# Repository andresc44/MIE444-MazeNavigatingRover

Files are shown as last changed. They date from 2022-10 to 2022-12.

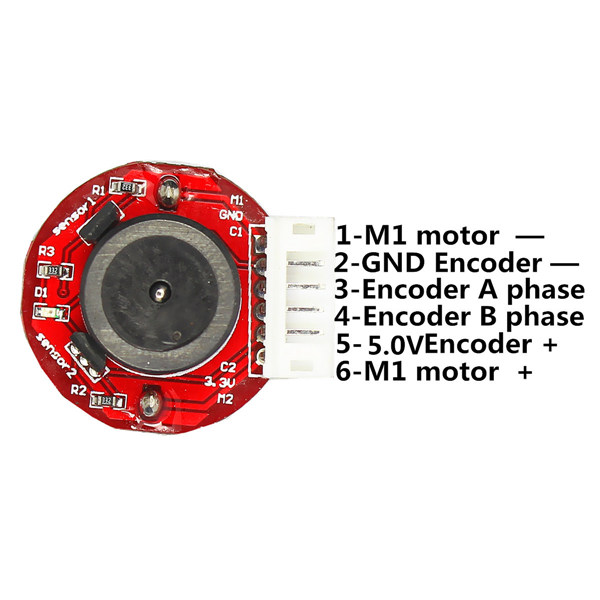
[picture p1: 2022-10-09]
Documents/SampleCodes/Encoder/6V_DC_Motor_Encoder_Wiring.jpg

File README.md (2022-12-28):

# MazeNavigatingRover
**Mechanical Engineering students of MIE444 at the University of Toronto**

*Andres Cervera Rozo, Christopher Tong, Liam Toner, Nathalie Cristofaro*

## Description
Course project to autonomously navigate through a maze and retrieve a wooden block

***Enter Summary of project, contest, 3 milestones, and key words of our design***
- 360 degree Lidar
- 3 Omni wheels for holonomic movement
- Hector SLAM for mapping area
- AMCL and move_base for localization and navigation to various waypoints
- Gazebo simulation of maze for parameter tuning
- Servo motor to retreive a block based on a Time of Flight sensor
- 3 DC Motors with encoders for straight motion tuning
- LED feedback
- Laser-cut plywood chassis
- 2 Arduino UNOs for rapid microcontroller response
- Raspberry Pi for communication to remote ROS Master
- 3D-printed sensor mounts and block retrieval mechanism

[Final document](https://github.com/andresc44/MIE444-MazeNavigatingRover/blob/main/Documents/MIE444%20Final%20Report.pdf)

[Project Proposal](https://github.com/andresc44/MIE444-MazeNavigatingRover/blob/main/Documents/MIE444_Proposal_Team_11.pdf)

## Autonomous Rover


## Course Maze


Please view this video to view the successful completion of the first milestone
[Trial Video](https://drive.google.com/file/d/1N6VmtPNb4CGCVo7hIk6XC2uphVTjW1oM/view?usp=sharing)

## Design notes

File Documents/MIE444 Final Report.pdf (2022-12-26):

## MIE444 - Mechatronics Principles

## Final Project Report

December 16th, 2022
Group 11

Liam Toner (1005178754)
Chris Tong (1005661874)
Andres Cervera-Rozo (1005469217) Nathalie Cristofaro (1004838009)

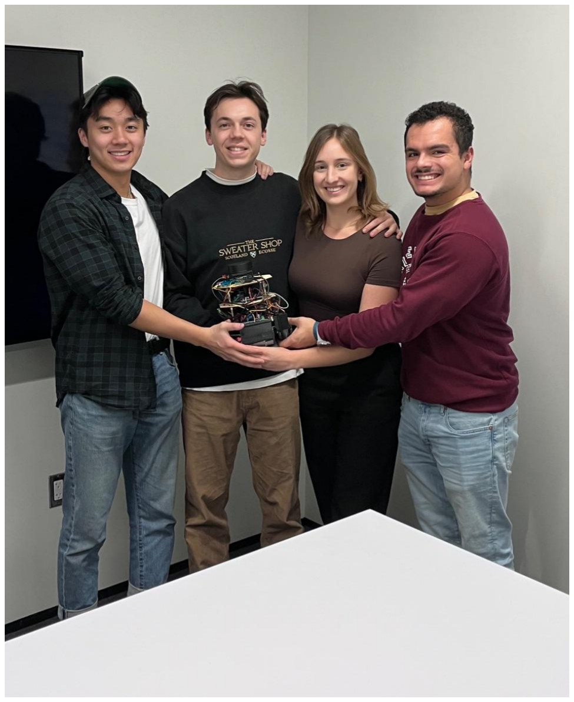
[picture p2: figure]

Link to milestone 3 videos: https://drive.google.com/drive/folders/1ZH4aUpbSbr8QGiYuTMWXnF71OBrIfj4q?usp=s haring (https://drive.google.com/drive/folders/1ZH4aUpbSbr8QGiYuTMWXnF71OBrIfj4q?usp=sharing)

## Table of Contents

1.0 Executive Summary | 2
2.0 Detailed Rover Control Strategy | 2
2.1 Obstacle Avoidance Strategy | 3
2.1.1 Component Software and Integration | 3
2.1.2 Movement Strategy | 4
2.1.3 Calculating and Generating Movement Commands | 4
2.1.4 Milestone One Challenges and Solutions | 5
2.2 Localization and Navigation Strategy | 5
2.2.1 Creating Simulation in Gazebo | 6
2.2.2 Introduction to Hector SLAM | 8
2.2.3 AMCL ROS Package | 8
2.2.4 Sending Navigation Goals Node | 9
2.2.5 Move_base ROS Package | 9
2.2.6 Trajectory Planner, a Move_base Sub-Package | 9
2.3 Block Delivery Strategy | 10
2.3.1 Design of Block Retrieval Mechanism | 10
2.3.2 Programming Block Pickup and Dropoff | 11
2.4 Integration Strategy | 12
3.0 Final Results | 14
3.1 Obstacle Avoidance | 14
3.2 Localization | 14
3.3 Pick-up and Delivery of the Load | 14
3.4 Integration | 15
4.0 Discussion | 17
4.1 Obstacle Avoidance and Localization | 17
4.2 Robot Design and Assembly | 17
4.3 Electrical System Discussion | 18
4.4 Gazebo Simulation | 19
5.0 References | 20

## 1.0 Executive Summary

This report investigates the performance of group 11’s robot for the Mechatronics Principles course term project. The project consisted of designing, building, and programming a robot that would complete three milestones throughout the semester.

The first milestone was obstacle avoidance, where the robot had to travel 20ft in a maze without hitting walls. The team’s robot completed this challenge successfully, with the robot only needing one adjustment to continue on its course. In order to complete this achievement, the team used a Raspberry Pi, LiDAR sensor, and an Arduino Uno to control the robot systems, with the Raspberry Pi acting as the main controller. The Raspberry Pi and LiDAR communicated with a remote PC through the ROS framework to determine the direction and response of the robot. The PC would send PWM values to the Arduino Uno through the Pi to control the direction and speed of the omni-wheels.

The team was not able to complete the second milestone, which involved navigating and localizing in the maze, due to the short timeline available to debug the Hector SLAM mapping package. However, the initial plan to complete this task was to model the robot as a URDF file, use Hector SLAM to map the maze, and use AMCL to create a particle distribution probability map that would determine the final location of the robot by comparing a live map with the pre-generated reference map. A Gazebo simulation was intended to be used for debugging and as a back-up plan to show the robot localization in a simulation.

The third milestone combined the previous milestones and added the additional challenge of locating and delivering a block. The robot was able to successfully complete the third milestone by combining the original idea for milestone two with some alterations to facilitate the programming. A sweeping mechanism was added to the robot frame, which was able to efficiently acquire, contain, and deliver the block to a drop off location. The robot was also capable of localizing at the four-way intersection in the maze.

Overall, consistent with the agreed upon goals at the start of the project, the team learned a great deal about Hector SLAM, ROS architecture, and other common packages and frameworks used commonly in the mechatronics industry. The physical design of the robot was very successful, whereas programming posed a few challenges that would have been resolved with more time, or if the team had chosen a simpler robot design and concept for the project.

## 2.0 Detailed Rover Control Strategy

If the reader is not familiar with ROS, in order to comprehend the terminology in the following sections of the report, the team has recommended the following online references which provide definitions for terms such as node, topic, publish, subscribe, etc. and general information on the ROS framework used for this project.

Online resources:
[1] https://wiki.ros.org/ROS/Introduction
[2] https://ros.org/

## 2.1 Obstacle Avoidance Strategy

In order to complete milestone one, the robot needed to achieve an efficient obstacle avoidance strategy to navigate through the maze without colliding into walls. The robot accomplished milestone one using a LiDAR sensor, remote master PC, Raspberry Pi, and Arduino to collect and send data to the motor controllers which controlled three DC motors with encoders, each attached to an omni-wheel.

2.1.1 Component Software and Integration
The Raspberry Pi is essentially a small computer that is compatible with multiple distributions of the Linux operating system. The team’s Raspberry Pi used the Ubuntu 20.04 distribution in conjunction with the Robot Operating System (ROS) framework. The ROS framework is a free open-source software that defines the various tools, libraries, and interfaces used to connect to the actuators and control the systems of a robot. The use of this framework facilitated the integration of a LiDAR sensor into the robot design, which would typically be very complicated without utilizing pre-built libraries. The Raspberry Pi comes with an integrated wifi connectivity option, which the team used to connect to an external PC. The external PC used by the team was dual-booted in order to use Linux as a second operating system. The PC’s Ubuntu system also had the ROS framework installed. Once the Raspberry Pi and external PC were confirmed to be on the same wifi network, the bashrc files were configured to link the IP addresses of both devices; the PC was set as the master and the Raspberry Pi as the slave so that the Raspberry Pi could be controlled from the PC.

The LiDAR was connected to the Raspberry Pi using a standard USB cable. The Pi would take in the raw LiDAR data and convert this data into a Laser Scan message which was published to a /scan topic. This procedure would transform the data into a global variable that could be read by the PC. The PC accessed this data by subscribing to the /scan topic.

2.1.2 Movement Strategy
The LiDAR sensor gathered data by taking 720 distance and angle measurements during one full 360° rotation. This data was sorted into a 720 element array which was divided into a 12 section circular map, as seen in Figure 1.

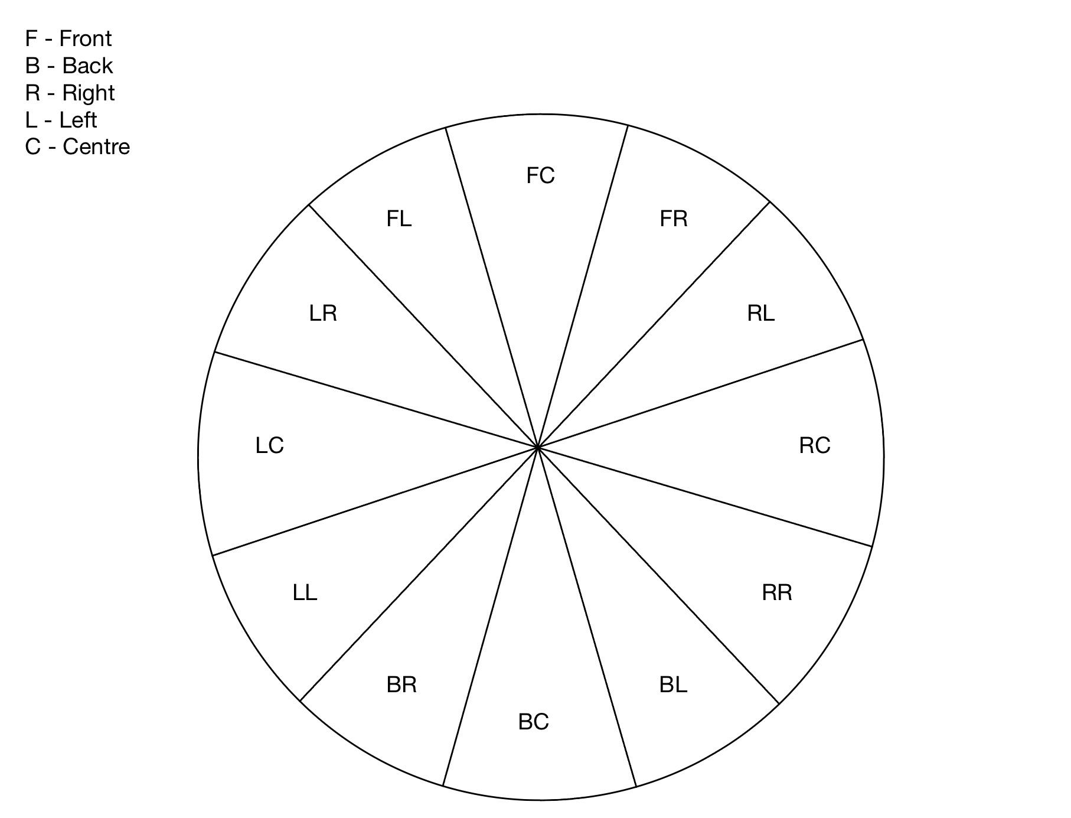
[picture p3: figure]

Figure 1: LiDAR Map Visualization.

Each slice of the map contained 60 data points that helped the robot determine if an obstacle was present in the region. The robot was designed to move in such a way where the front-center slice was always the preferred movement direction. If an obstacle was not detected by the LiDAR in this region, the Arduino would send a “move straight” command to the motor drivers and the robot would move forward. If an obstacle was present in the front-center slice, the robot would check if obstacles were present in the next two outer slices, and continue around the circle until an obstacle was not detected in one of the slices. Once a slice with no obstacle was found, the Arduino would send a “rotate” command, and the robot would align the front-center slice with the slice that contained no obstacles before moving straight. If every slice contained an obstacle, the robot would rotate and move in the direction of the furthest obstacle.

2.1.3 Calculating and Generating Movement Commands

The output of the obstacle avoidance algorithm used in the robot movement strategy was a command velocity that would either indicate that the robot needed to rotate or drive straight. As there were three omni-wheels and because the wheels were multi-directional, the node that received the command velocity performed matrix multiplications in order to convert the command velocities into a pulse width modulation (PWM) magnitude and rotation direction for each wheel based on their geometric configuration. These calculations were done on the PC and transmitted to the Raspberry Pi, which was connected to the Arduino using serial communication. The Pi ran a script to ensure that the Arduino was subscribed to the relevant topic, and published data accordingly. The gathered PWM signals and rotation directions were combined into a smaller 6 item array message that was received by the Arduino. 1s and 0s in the message would indicate whether the wheels would need to turn clockwise or counter-clockwise, respectively. These direction commands were sent to the motor controller via digital write pins on the Arduino. The PWM signals in the message were sent to the motor’s enable pins via the analog write pins on the Arduino, and these signals would determine the motor speed. The LiDAR data retrieval and communication with the other components occurred at a speed of 10Hz, which explains why the robot movement was smooth and efficient.

2.1.4 Milestone One Challenges and Solutions
For the robot to effectively avoid obstacles, some obstacle avoidance script parameters were created in the code which helped the robot determine when it should begin turning depending on its footprint size. These parameters also helped the robot drive straight, since they would regulate how close the robot should be to walls while it was driving. By adjusting these parameters, the team was able to more effectively avoid the maze walls; however, the wheels would often graze corners as it was difficult to find the correct parameter balance. In addition, the wheel PWM signals had to be individually adjusted to account for some motors which spun faster than others at the same PWM. By adjusting these signals, the robot was able to drive straight when it was not surrounded by obstacles.

## 2.2 Localization and Navigation Strategy

Milestone two required the same hardware from milestone one along with a second Arduino to control the LEDs that indicated robot localization and position in the maze. The communication between components was the same as in milestone one, however the source of the command velocity topic was different. The team was unfortunately unable to complete milestone two, however the following sections describe the original plan the team devised for this milestone. The team ended up using a different procedure for localization and navigation due to time constraints and coding complexity, which is discussed in Section 3.0.

2.2.1 Creating Simulation in Gazebo

In order to localize and navigate inside of the maze, it was faster to test the code inside of a simulation as opposed to relocating to a physical maze every time. Additionally, simulation was not limited by battery life, there were no hardware bugs, and the same code could be used for simulation and real life. Although most teams opted to use Matlab for their simulation, ROS integrates better with Gazebo: a 3D robotics and physics simulation software. Since Gazebo is open source, there are many readily available plugins that allow for the simulation of different sensors like LiDAR and TOF (time of flight). The role of Gazebo in this project was to test and visualize the LiDAR, the obstacle avoidance code, the localization code, and the pick up mechanism code. This section describes some basic terms and the process that was used to set up the simulation in Gazebo.

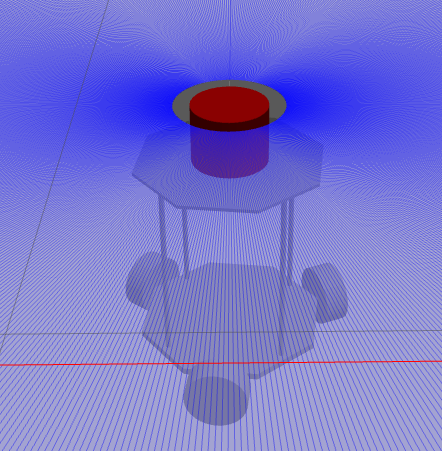
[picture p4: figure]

Figure 2: Robot URDF with Red LiDAR in Gazebo.

In order to import objects into Gazebo like the robot and maze, the objects must have a unified robot description format (URDF) file type (see Figure 2): a file format that describes the physical properties of an object like weight, center of mass, and dimensions. Mechanical engineers are familiar with using CAD to model 3D objects, however, a URDF file is generated using a coding language called extensible markup language (XML). To make the task simpler, Solidworks was used to model the robot and then a Solidworks plug-in was used to convert the CAD file (.sldprt) into a URDF file (.urdf). From there, the bulk of the code was generated by the plug-in and small tweaks to the code to specify the linkage masses, moments of inertia, and visual representation were added. A collision box around the robot was also defined, which specified the allowable movement radius of the robot body before it would collide with obstacles in the simulation. Each linkage was also given a separate central coordinate system so that the link movement could be modeled relative to the robot in the graphical user interface (GUI) of the URDF plug-in.

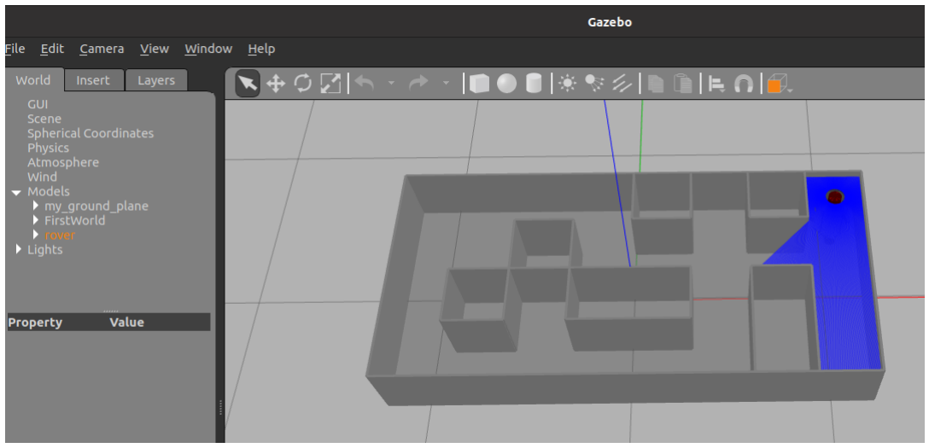
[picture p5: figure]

Figure 3: Gazebo Generated Maze (robot with LiDAR seen in top right of maze and blue highlight represents the field of view of the LiDAR).

The maze was created differently, using the editor tool in Gazebo, the team created a scaled maze with walls in the same positions as the course’s maze (see Figure 3). Two plugins were then added to the URDF to better simulate the design; libgazebo_ros_laser.so to simulate LiDAR data and record it in /scan (see Figure 4) and libgazebo_ros_planar_move.so to represent the omni-wheel drive system of the robot. In order to localize the robot in the simulation, the /scan data was read by the AMCL ros package (more on this in 2.2.3). A robot’s pose describes the robot’s position in a space. In this case, the robot operated in a three-dimensional space and thus had six degrees of freedom: three cartesian (x, y, z) and three angles (roll, yaw, pitch). Any time the robot would need to change poses, an original reference position as well as a final position was needed. The drive system plug-in accepted command velocities from a topic and moved the robot (in x, y, z, roll, yaw, pitch velocities where z, r, y are zero) based on the pose changes in the Gazebo simulation. A launch file was then created to spawn the robot URDF inside of the world (maze) created at a predefined location.

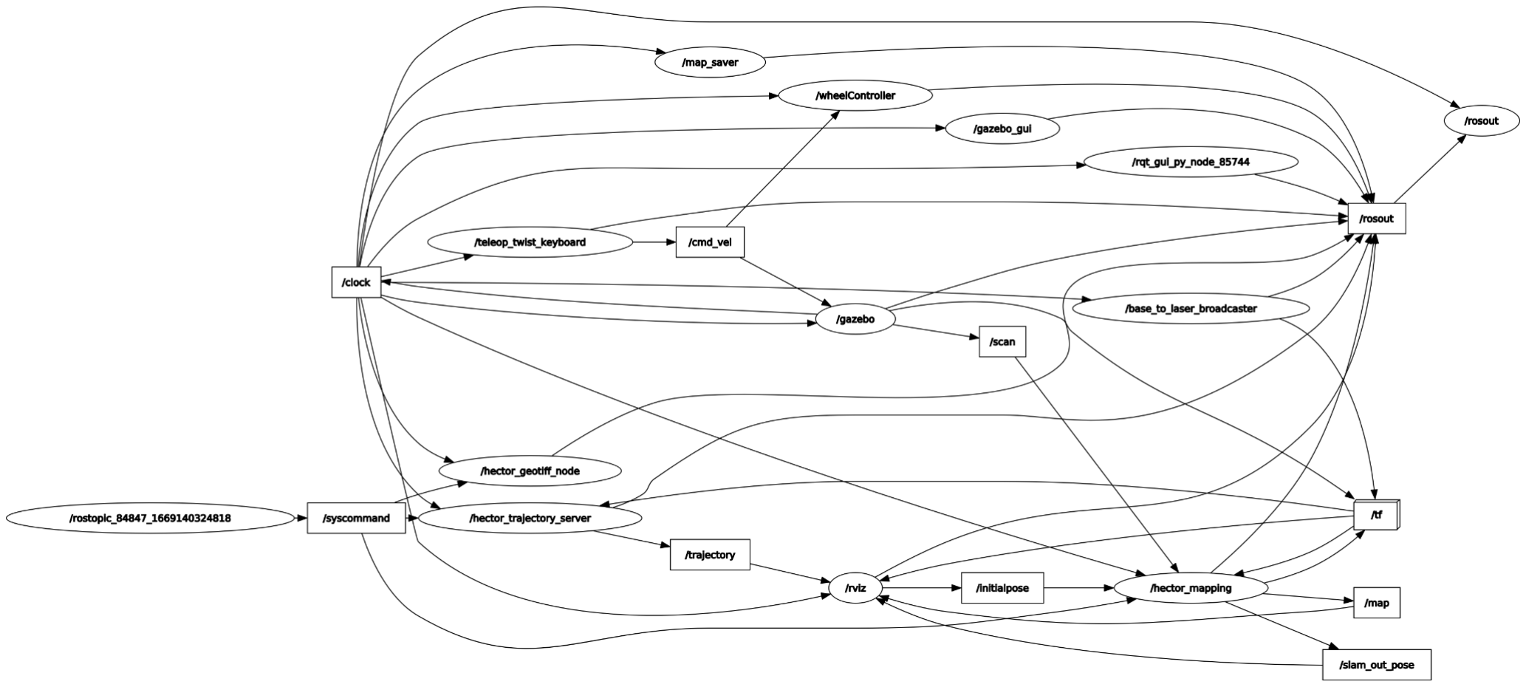
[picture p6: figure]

Figure 4: Node Network of Hector SLAM Operating with Gazebo Simulation.

2.2.2 Introduction to Hector SLAM

The Hector Simultaneous Localization and Mapping (SLAM) package was installed in ROS, which mapped an environment as a grid map and improved the accuracy of robot navigation. Hector SLAM used LiDAR data to create an iterative scaled reference map of the environment that the robot was in. Hector SLAM created a transform between the LiDAR laser frame of reference (FOR) and the map FOR, to create a map that was free of noise from the motor movement. The map was fully generated by manually driving the rover across the maze to map every area. This map was saved locally to memory, to be used for future localization.

2.2.3 AMCL ROS Package
The adaptive Monte Carlo localization approach (AMCL) was chosen as the means by which to localize the robot based on purely LiDAR data. AMCL is a probabilistic localization system that uses a particle filter to track the pose of the robot relative to the Hector SLAM reference map. The dispersed particle cloud created by the AMCL algorithm contained all the possible locations of where the robot could be in the maze at that instance. As the robot would advance through the maze, this cloud would converge to a centralized location and orientation by matching the LiDAR data to the existing map. This output pose was a position coordinate array (in x, y, z, roll, yaw, pitch coordinates) of the most probable location of the robot in the maze. This AMCL pose was refreshed up to 10 times a second with a new pose, where the probability of the robot being in this specific pose was adjusted after each update. All the relevant package parameters such as the number of particles, LiDAR height scan, etc. could be configured for this specific application.

This pose was then overlaid onto the reference map using RViz: a GUI tool that visualized the surroundings of the robot based on multiple data streams. The active localized map was displayed in RViz in real time based on the incoming LiDAR sensor data.

2.2.4 Sending Navigation Goals Node
By using the map reference frame, a location on the map could be chosen as the final destination objective for the robot. In milestone two, the first objective was reaching the loading zone. The first navigation goal was the entrance to the loading zone. After having arrived and retrieved the block, the navigation goal would then change to one of the four drop off locations in the maze, and also specify the final position and orientation of the robot. The four states of operation (navigating to loading zone, loading, navigating to drop off zone, and unloading) were represented by different color LEDs that were controlled by the Raspberry Pi GPIO pins.

2.2.5 Move_base ROS Package
The move_base ROS package handled the movement of the robot towards the current navigation goal. The move_base package created the live cost maps of the system, which assigned a cost to each obstacle and an inflated region around them. There are two types of cost maps: global and local. The global cost map was based on the Hector SLAM reference map, and assigned a cost of 1 to the walls (should be avoided entirely). Each wall also had an inflated radius, which represented an area that could be entered but would be preferably avoided, and had a cost between 0 and 1 (could be a viable route region if there are no alternatives). The inflated radius used in the software was 40mm. The local cost map was generated with a radius of 2ft around the robot based on the live LiDAR data of the robot, which helped the robot avoid nearby obstacles. For both types of cost maps, the relevant parameters were configured as YAML (Yet Another Markup Language) files; a data serialization language used to create configuration files for any programming language.

2.2.6 Trajectory Planner, a Move_base Sub-Package
Move_base contained a subpackage called trajectory_planner. The input to this subpackage was a navigation goal and the output was the path that the robot would follow to arrive at the destination. The output path had curvature to avoid obstacles in the most efficient and ‘inexpensive’ way. Trajectory_planner used information about the robot footprint, cost maps, and limitations of the robot accelerating and turning speed.

The robot was instructed on how to move on the path using the command velocity topics, which were 6-element arrays (with velocities in x, y, z, roll, yaw, pitch). The Trajectory_planner adjusted to the movement of the robot and updated the desired path and the respective command velocity at a rate of 10Hz. These command velocity messages were converted to PWM signals for each wheel using the same transformation matrix as in milestone one.

## 2.3 Block Delivery Strategy

The team was able to complete milestone three, however used a different procedure than what is described in Section 2.3.2 due to time constraints and coding complexity. Section 2.3.2 describes the original plan for the programming structure, whereas the adapted plan inspired from the team’s original idea can be found in Section 3.0.

2.3.1 Design of Block Retrieval Mechanism
The final block retrieval mechanism consisted of 4 components: the ramp, two arms, and the sweeper. A TOF sensor was used to assist in block detection, and a servo motor was used as the sweeper actuation method. The ramp was mounted on the first layer of the robot using two 3D printed brackets. The ramp contained a slot where the TOF sensor was mounted within a cutout in the ramp such that the block sliding up the ramp could not hit the sensor. The two arms held the servo and sweeper, and were mounted to the second layer underneath the motor controllers. The servo connected to a long stand-off, which slid through the sweeper and into the arm on the opposite side.

The sweeper was epoxied to the stand-off, and the stand-off was attached securely to the servo using thread-locker. The sweeper design was curved to allow for a smooth scooping of the block. At the end of the sweeper, beauty blender sponges were secured to the sweeper, and served as flexible grippers to ensure that the mechanism didn’t jam and that the block didn’t catch on its ascent up the ramp. The ramp was at a 30˚ angle, which was chosen after prototyping mechanisms at various angles and selecting the most effective angle for both block retrieval and expulsion. Figure 5 shows the final design for the robot with the labeled block retrieval mechanism components.

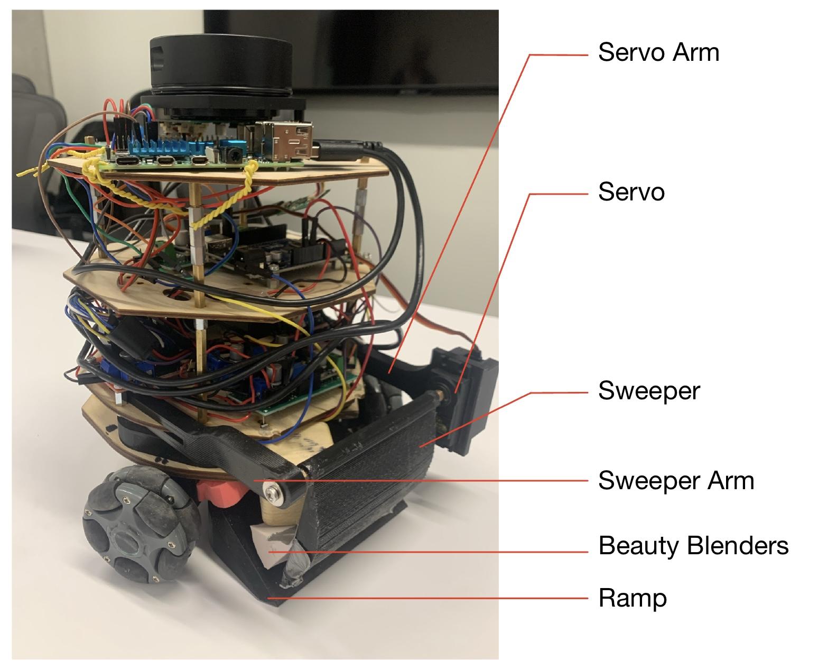
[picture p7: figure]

Figure 5: Final Robot Design.

2.3.2 Programming Block Pickup and Dropoff

The Arduino was connected over an Inter-Integrated Circuit (I2C) communication protocol to talk to the TOF sensor. I2C allows multiple peripheral circuits to communicate with one or more microcontrollers. There were no filters applied to the incoming TOF data, as it was already in digital form. Although it would have been ideal to output a filtered moving average of the data, this proved unfeasible due to the memory limitations of the Arduino UNO. The data from the TOF sensor was in millimeters, and it was published to a topic on the ROS network over ROS serial through the Pi. Once the robot achieved the loading zone navigation goal, the robot mode switched and was disconnected from navigation mode to stop auto-driving. The robot entered scan mode, which involved rotating and scanning the zone until a difference between the LiDAR front angle and TOF sensor was detected. This discrepancy in distance ensured that a block, and not a wall, had been detected by the robot. Once the block had been detected, the robot drove forward slowly until the TOF sensor detected that the block was around 40mm away. The servo controlling the sweeper would activate to bring in the block. The servo during this time was subscribing to a topic that was sending the PWM state the servo should operate at. After retrieving the block, a new navigation goal was set at the unloading zone. The robot followed the set path to one of the four potential unloading zones based on a parameter defined prior to the trial. When the robot arrived at the zone, the trajectory_planner outputted a message that the robot had arrived at the destination. The servo would be actuated once again, an LED would turn on, and the block would fall out, completing the final milestone.

## 2.4 Integration Strategy

In order to integrate obstacle avoidance, localization, block localization and retrieval, the hardware and software was iterated upon for each milestone. The plan was to have the following functions for each milestone:
Milestone 1: Reading LiDAR data and obstacle avoidance.
Milestone 2: Localization and obstacle avoidance.
Milestone 3: Localization, obstacle avoidance, and object pick up/drop off.

Since the team did not complete milestone 2, the main jump from was from milestone 1 to 3 and included the addition of the block retrieval mechanism as well as the code for the block search/retrieval. In order to control the hardware of the block retrieval mechanism (servo and TOF sensor) a second Arduino was added to the robot. The addition of a second Arduino and the components that came with it had been planned for since the beginning of the project. Space was allocated on the third level of the robot for the second Arduino along with the power supply needed for the servo, and 5V power for the Arduino was ready and waiting for its arrival after the initial buildout of hardware in milestone one, facilitating a smooth integration process of new functionality.

To ensure that the different functions worked harmoniously, the code for milestone 3 was divided into four modes so the robot functioned as a “state machine”:
Mode 1: AMCL localization and navigation to loading zone.
Mode 2: Block searching and pickup.
Mode 3: Navigation to drop off zone.
Mode 4: Block drop off at drop off zone.

All of these modes were set off by different “if” statements in the code and each mode was coded as a separate function so that it was easier to debug. What enabled all of these separate functions to integrate together was the ROS structure; all the nodes were constantly listening and publishing to topics that other nodes could listen to, so as soon as the if condition was met, a function knew whether to start or stop.

When placed in the maze, the robot starts off in mode 1, it localizes and drives to the entrance of the loading zone based on the navigation goal. Once the robot reaches the entrance of the loading zone, it enters mode 2. In mode 2, the robot rotates in place to search for the block. While rotating, values from the TOF and LiDAR are collected to record when a block is detected. If no block is detected, the robot drives 4 inches into the loading zone and rotates in place again to search for the block. Driving deeper into the loading zone ensures that the block is not obstructed from view during the first rotation. If the difference between the 0th degree of the LiDAR and TOF measurement is greater than the displacement between the sensors, the block is presumed to be straight ahead. In this state, the robot drives forwards towards the block and once the ramp makes contact with the block, the servo motor actuates to capture the block. Once the block is onboard, mode 3 is triggered and the robot drives to the drop off zone (relocalization was not necessary, since localization was continuously running in the background). When the robot reaches the drop off zone and the block is released, mode 4 is triggered and the delivery would be considered completed and successful.

## 3.0 Final Results

## 3.1 Obstacle Avoidance

In milestone one, the robot was able to avoid most obstacles present in the maze, only needing to be manually adjusted once when it got stuck on a corner. This incident occurred because the obstacle avoidance algorithm did not account for the robot’s physical width when a narrow, but clear path appeared at a specific point in the map with a zig-zag wall pattern. The plan outlined in Section 2.1 proved to be very effective for this milestone. Overall, the robot excelled in obstacle avoidance.

## 3.2 Localization

The robot was unable to complete milestone 2, as the code was not ready in time for the trail. The team had issues getting Hector SLAM configured to the odometry frame of the system, as well as to the frame of the LiDAR coordinate system, and instead decided to focus their efforts on the third milestone. As a result, the team did not attend milestone two, and the final results are discussed in Section 3.3.

## 3.3 Pick-up and Delivery of the Load

Figure 6 shows the OnShape model of the block retrieval mechanism (note that the sweeper is version 3, which is not the same version used in the maze). In Figure 6, “1” represents the block, “2” represents the sweeper mechanism which was powered by a servo motor, and “3” represents the ramp where the block was stored.

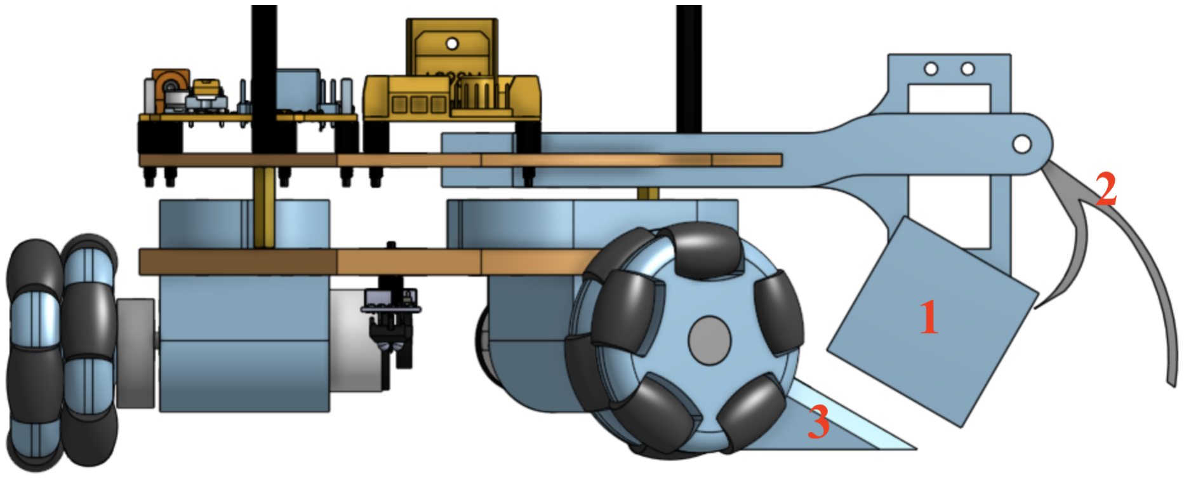
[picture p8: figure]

Figure 6: OnShape Model of Block Retrieval Mechanism.

The team was able to complete the third milestone using most of the procedure described in Section 2. However, a few alterations to the original plan were required, as the team could not get all the parts of the program to function fully for the milestone. In order to complete the milestone, the robot was programmed to localize at the four-way intersection of the maze, where it could navigate to the final drop-off zone. This was achieved by collecting LiDAR data at the four-way intersection and creating an if statement such that if the outputs of the scan topic ever resembled that of the intersection, the robot would localize at the intersection. This was the only section of the maze where the robot could reliably localize. To begin the milestone, the robot entered a general navigation mode and constantly searched for the block by comparing the distance of the LiDAR sensor with the TOF sensor distance. If the TOF sensor distance was ever less than the LiDAR distance, this meant the block was detected. Once the block was detected, the robot would approach the block slowly and sweep it in once the TOF distance was less than 90mm. After obtaining the block, the robot navigated around the maze to find the four-way intersection. At this intersection, the robot drove to the final drop-off zone and deposited the block.

There were a few instances where the TOF sensor detected a block when in reality, it was a corner of the maze; this issue is further discussed in Section 4. Otherwise, in the first attempt, the robot was able to find, pick-up, localize, and deliver the block. In the few minutes of the attempt, the robot entered block detection mode (mode 2) prematurely due to the TOF confusing walls with the block, so the robot had to be pushed into the loading zone since this mode of operation does not navigate autonomously around the maze. In the second attempt, the robot was able to make it to the loading zone, obtain the block, and properly identify and stop at the dropoff point, but was unable to unload the block after localizing. When combining the two attempts, the robot was able to demonstrate that it could localize, pick-up, and deliver the block to a drop-off location, and thus the team successfully completed the final milestone objectives.

## 3.4 Integration

The team was able to effectively integrate the components from each milestone and add new features through extensive planning during the design proposal stage. Between milestone one and three, the block retrieval mechanism, new hardware, and new driving modes were added.

To add the block retrieval mechanism, the spacing of the components was organized during the initial OnShape modeling of the design. As much space as possible was left at the front of the robot to allow for flexibility when designing the mounting for the ramp. Mounting the sweeper was also successful, as there was space left underneath the motor controllers on the second layer. It was difficult however, to disassemble the sweeper arms from the robot, as the motor controllers would have to be removed first.

Adding additional hardware such as the sweeper servo, second Arduino, and TOF sensor was also planned for in both the design layout and when creating a wiring diagram. Wire routing cut-outs were used to route the new components neatly into the pre-existing design. The wiring diagram proved to be very helpful, as the team knew the number of required pins for each component, could plan ahead when sizing the DC-DC converters, and used the diagram as a reference when adding to the electrical system between milestones.

The software side of the robot was also continuously reiterated and repurposed, allowing for integration between milestones. The original script for converting velocities to PWM signals and the first Arduino code to control the motor PWMs were both reused for the second and third milestones. The main change for the third milestone was how the command velocities were generated in coordination with the LiDAR sensor. In addition, to conceptually plan out the programming, a ROS nodes block diagram was created in the initial design proposal to understand the tasks and progress the team needed to complete between each milestone.

Overall, the team achieved effective integration of the programming and design components between the three milestones through extensive planning and thoughtful methods of organization.

## 4.0 Discussion

## 4.1 Obstacle Avoidance and Localization

The overall obstacle avoidance strategy proved to be successful, with the exception of 1 specific edge case that required additional assistance to turn the corner. The high rate of velocity commands ensured that the robot was driving smoothly by making minor changes to its direction when driving straight. A future consideration would be to increase the angle range of the ‘forward direction’ that needs to be clear of obstacles in order to move forward. This would ensure that a narrow, but clear path would not be considered viable.

Although the overarching localization and navigation pipeline was completed in time, the actual performance of the localization proved to be unreliable. The AMCL package required an odometry frame as an input so that it could track the robot’s movement and adjust the particle cloud accordingly. Because the encoder data was not linked to the ROS network, a laser-based odometry package named laser_scan_matcher was used. Although there should not be a drift in the laser based odometry frame, the resulting localization output of AMCL jumped across the map as the robot moved, causing the cloud to require an extensive amount of data before localizing. The source of this jump was not identified. A further investigation into the accuracy of the odometry to map transform would be required to address this issue. Alternatively, this issue may have been addressed by using an encoder based odometry solution. The motivation against utilizing encoder data for odometry initially was due to the potential for drift to accumulate throughout the course.

Had the robot been able to localize in a more efficient manner, the pipeline was ready to navigate autonomously to any chosen point on the map.

## 4.2 Robot Design and Assembly

The final mechanical design for the robot proved to be very sturdy, highly effective, and well organized. There were no iterations required for the main structure, wheel mounts, battery mount, or ultrasound brackets. The robot was sturdy due to the lock nuts used to fasten all the brackets, which ensured that connections would not loosen over time. All the electrical components were mounted on standoffs to ensure proper air flow and prevent overheating, which was one of the design strengths considering all components had proper ventilation. The main structure of the robot was made of laser-cut plywood which had various cutouts that could be used to route wiring for organization. Any holes for mounting brackets were also already added in the OnShape file so that drilling would not be required, making assembly easy and efficient.

The wheel mounts ensured that the omni-wheels were each at a 120˚ angle from each other. These wheel mounts were secured to the base layer with screws and locknuts, and the motors connected to the wheels using a connector on the shaft. For the wheel shaft mounting system, the team would recommend using either metal or wood for the shaft mounts, as the fastening strategy used to secure the motor shaft to the wheel had a nut eating away at the edges of the 3D printed material. To resolve this temporarily, the team placed small slices of sheet metal on either side of the nut so that it would not damage the mount further.

The sweeper mechanism required a few iterations for the flap; however, in the end the team used the first iteration and taped beauty blenders to the tip. The beauty blenders added some grip to the sweeping mechanism so it would effectively grip/tip-over the block when the flap came into contact with it. The flexibility of the blenders ensured that the block could be swept in while being oriented at various angles.

The sweeper design had some flaws including occasionally unscrewing from the servo when hitting the block during intake, TOF sensor placement issues, and requiring that the standoff be epoxied to the 3D printed sweeper. To resolve the unscrewing issue, the servo should be mounted on the opposite side of the robot so that block intake can only tighten the screw connection. The TOF sensor should also be mounted so that it is angled correctly to ensure that the block is detected at further distances, which can be done by angling the screw holes or ensuring the ramp is level. The standoff should be either press fit into the sweeper or a heat gun could have been used to have the 3D printed material flow around the standoff to secure it.

One major feature that could be redesigned is the footprint of the robot, as it was larger than expected which made it harder for the robot to turn. The omni wheels and sweeper mechanism were the main causes for the larger footprint. An improvement would be to integrate the sweeping mechanism into the body of the chassis so that it doesn’t protrude as much from the structure. Space could be made by mounting all the motor driver electronics on vertical walls instead of mounting them horizontally on each layer.

## 4.3 Electrical System Discussion

The final electrical design of the rover was effective and reliable, but could have used some improvement in user friendliness/ease of use. Throughout the project, the team experienced no electrical incidents, and no components were damaged as a result of improper wiring, incorrectly spec’d parts, etc.. All components received adequate current and voltage supply, and pin allocation was kept consistent throughout the project to avoid confusion. More robust electrical connectors and/or harnesses would have made the design less precarious, however, the team made the most of the materials and budget which were available.

Part of what made the electrical system so robust was the care that was taken in ensuring that all components on the robot were being powered by a supply with adequate voltage and current capacity. For example the Raspberry Pi needed a dedicated 5.1V, 3A buck converter. Had this not been accounted for, the Pi would not have been able to operate properly and the entire robot would cease operation. Additionally, the servo motor used in the block retrieval mechanism had a stall current of 2.5A, so it too needed a dedicated power supply to prevent drawing excess current from, and frying the Arduino which controlled it. The electrical requirements for this project were not overly complex, but since the design was constantly in flux (frequently being assembled/disassembled) the team was reminded of the value of a consistent electrical layout. Getting electrical sorted out early allowed for more resources to be allocated to the more complex part of this project for the team - the software.

An improvement which could have been made would be adding standardized quick disconnects (Molex connectors or something similar) for the wires traveling between layers of the robot structure. This would have allowed for the layers of the robot to be more modular, and eliminated any worry that wires were being reconnected erroneously between the many disassembly/assembly cycles as the robot was iterated on. All things considered though, the electrical system was thoughtfully planned early on, executed well, and met all necessary requirements throughout the entire design process.

## 4.4 Gazebo Simulation

The Gazebo simulation was functional in providing a world environment to test the inputs and outputs of each subsystem rapidly without needing to boot the robot and launch the files. The simulation rover was able to respond to command velocity commands and output live LiDAR data about the maze. The goal of the simulation was to create a test setup where the various parameters of the localization and navigation packages could be rapidly configured and tuned to this specific application. Because the robot was not able to localize using the AMCL package, the full capabilities and benefits were not realized.

Had the original localization plan worked, the simulation would have identified any potential logical issues in the navigation strategy. Additionally, a TOF sensor would have been integrated into the simulation to test the identification and retrieval of the block in the loading zone.

## 5.0 References

[1] Dattalo, A. (2018, October 8). ROS/Introduction. ros.org. Retrieved December 11, 2022, from https://wiki.ros.org/ROS/Introduction
[2] ROS - Robot Operating System. ROS. (n.d.). Retrieved December 11, 2022, from https://ros.org/

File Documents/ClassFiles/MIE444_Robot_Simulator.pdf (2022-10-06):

# SimMeR

# Simulator for Mechatronics Robots

Version 0.2

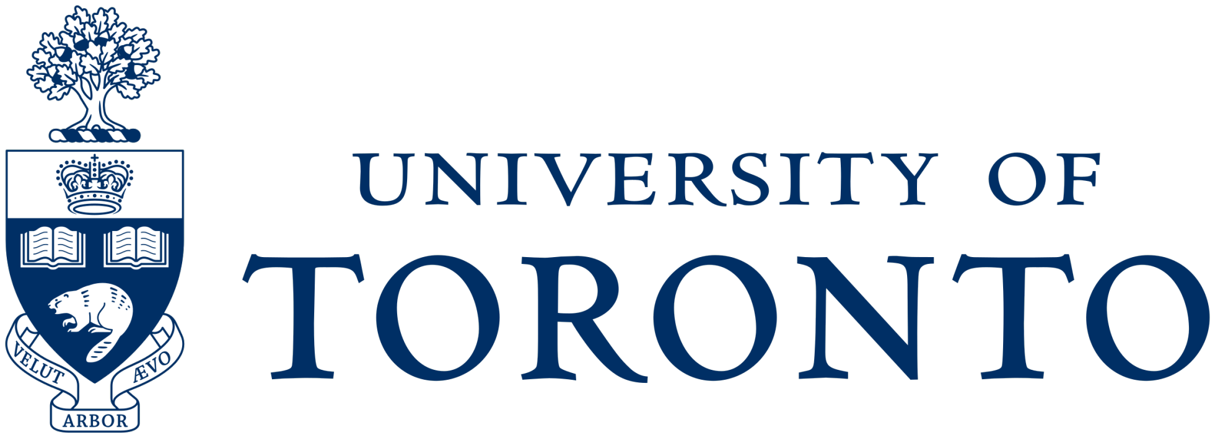
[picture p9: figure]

### Ian Bennett

Developed for the University of Toronto Department of Mechanical and Industrial Engineering

## Contents

1 Abstract | 3
2 Change Notes | 4
3 Introduction | 5
4 Configuration Files | 8
4.3.4 | Column D-F - X-Position, Y-Position, Z-Position . . . 12
4.4.4 | Column D-F - Y, X-Axis Error & Rotation Error . . . 15
5 Simulator User Guide | 17

1

2

## 1 Abstract

This document presents the design and key features of a robotics simulator for MIE444 Mechatronics Principles. The simulator is a software tool written in MATLAB, designed to allow students to test navigation and localization algorithms remotely during the COVID-19 pandemic. The simulator provides software inputs and outputs for several different types of sensors and is plug and play compatible with a similar Bluetooth communication program used to send commands to a microcontroller on board a physical robot. Communication with the simulator is performed using TCP protocol, and is compatible with any programming language that can send and receive data in the correct formats, including MATLAB and Python.
The program begins by generating a maze and user robot from a number of user editable text files. These files will contain the maze wall locations, robot sensor suite and mounting locations, and control character mapping for the sensors and movement. Measurement and control precision is also definable by the user and can be configured to replicate the types of error seen in real world systems based on the configuration chosen by the user. The simulated robot is displayed on a plot, and all data from the simulator can be accessed by the user if needed.

3

## 2 Change Notes

### 2.1 Version 0.1

September 27, 2020

1. Initial Release

### 2.2 Version 0.2

October 16, 2020

1. Added ”Change Notes” section to this document
2. Completed ”Configuration Files” section of this document
3. Updated format of data returned by the simulator to single precision float
4. Added requirement for a newline character at the end of messages to simulator

4

## 3 Introduction

This simulator was created as part of a project for the University of Toronto Department of Mechanical and Industrial Engineering, for the course MIE444 Principles of Mechatronics. The program including all scripts, functions, files, and documentation are distributed under the GNU AGPLv3 license. The author would like to acknowledge the work of Douglas M. Schwarz, whose program intersections.m is used in this program. The license for intersections.m is available in the folder ”documentation” within the main directory.
SimMeR is written in MATLAB using version 2020a, the most recent version available at the time of creation. No packages other than the standard install are used aside from the instrument control toolbox (included in most standard and student licenses), which is used to communicate over TCP

with the simulator. Some open-source, freely available functions are used, including intersections.m, but only when they provide functionality that can’t be easily replicated using the standard installation.
The goal of the project component of the course MIE444 is to have students design and construct a robot to perform simple mapping and localization to autonomously collect a small object from within a maze and deposit into a predetermined zone.
To this end, students must program mapping and localization algorithms to take and fuse input data from a number of sensors and create output commands to control motors that will move the robot. The simulator provides an environment in which these algorithms can be tested without actually having to build the and operate it in the maze.

### 3.1 Program overview

SimMeR performs the following tasks as part of its initial setup.

1. Loads/generates the maze, including wall locations and checkerboard

5

locations.

2. From a user-defined text file, generates a simulated robot including size, shape, and sensor loadout and placement.
3. Creates a TCP server object to listen for commands from the control algorithm.
4. Creates a text file that data from each step the robot takes will be appended to for users to view and debug with (not yet implemented).

As part of its main command loop, SimMeR performs the following steps:

1. Accepts a TCP packet command from the control algorithm programmed in MATLAB, Python, or another language.
2. Funnels the packet to either the simulator or a Bluetooth serial port (not yet implemented) connected to a physical robot.
3. If using the simulator, parses the packet to extract the command code.
4. Search a user-defined lookup table to determine whether the packet is a telemetry request (i.e. to collect sensor data) or a control command

to move the simulated robot in a direction, then acts on the command.

a. For telemetry requests, these are passed to an appropriate function that simulates the response data packet of the desired sensor. The function takes into account the position of the simulated robot within the maze, generates the value that the sensor should read, adds noise based on a defined noise profile for that sensor, and constructs a return data packet that is identical to one produced by the physical robot’s microcontroller.
b. For control commands, these will be passed to a function that moves the simulated robot within the maze. The drive distance

6

and direction and/or the rotation value for the configuration is

specified by the user algorithm. Error is added based on a user-defined drive error profile, and used to update the simulated robot’s position. Several drive noise profiles will be preconfigured by the course teaching assistants based on common wheel/motor configurations (not yet implemented).

5. For a control command, the program generates a path based on the movement. If a collision is detected between the robot and the wall along the path, the program assumes that the robot stops moving at the collision point.
6. Based on the new location and/or rotation of the robot, positions of the sensors are updated. For integration-based sensors (such as gyroscopes and odometers), their values are updated based on the movement of

the robot and user-defined noise profiles.

### 3.2 Compatibility

In order to ensure that the user-created programs work with both the simulator and a physical robot, they both must take and interpret commands and respond to the environmental stimulus similarly. The input and output software interface are designed to be as similar as possible. To this end, in addition to the simulator, a Bluetooth command piping program will be created to pass data from the user program to a Bluetooth module on the physical robot (not yet implemented). The physical robots’ microcontrollers

should be programmed to read commands and output data over Bluetooth in the same way as SimMeR does for ease-of-use. For more information on data formats, see Section 5.5.1.

7

## 4 Configuration Files

This section details the various configuration files used by the robot simulator to do the following things:

1. maze.csv - Define the maze wall locations.
2. robot.csv - Define the user’s robot size and shape
3. sensors.csv - Define the sensor loadout, locations, error & definition parameters, and command codes.
4. drive.csv - Define the user’s robot’s drive system, associated error/bias

parameters, and command codes.

Note that the checkerboard pattern is not predefined in a config file. It is generated using a fixed-seed random number generator within the function import checker.m.

### 4.1 Maze Wall Locations

Relevant Files

1. maze.csv - maze definition configuration file
2. import maze.m - MATLAB function to import and create the maze

The file maze.csv in the config folder contains the definition for the maze walls. Maze walls are defined using a 4 row by 8 column matrix, with each cell containing a number between 0 and 3. Each of these numbers defines a 1 foot by 1 foot square in the maze as either an square surrounded by a wall (0), an empty square (1), a robot starting location (2), or a block location (3). If the maze dimensions are to be changed, this can be done by editing the

variables dim1 and dim2 in the import maze.m file, and adding additional rows/columns to the maze.csv configuration file.

8

The function import maze.m creates an n-by-2 matrix maze xy that defines the (x,y) perimeter points of each of the wall squares, each separated

by a pair of NaN values. The function begins by drawing an outer rectangle around the perimeter of the maze as defined by the dim1 and dim2 variables (the x and y dimensions of the maze perimeter, in feet), and stored

in maze xy. The imported data from maze.csv is iterated through, and for each square indicated as surrounded by a wall (value 0) a 1 by 1 foot

square is appended to maze xy via its perimeter points. Note that the corner points of the outer wall are added in a counter-clockwise order, and the corner points of each internal square is added in a clockwise order. This enables collision-checking functionality for the rover when it moves, later in the program.
Before passing the variable maze xy out of the function, it is multiplied by 12 to convert the dimensions from feet to inches.

### 4.2 Robot Shape

Relevant files

1. robot.csv - robot definition configuration file
2. import bot.m - MATLAB function to import and create the robot

The file robot.csv in the config folder is used to define the robot perimeter size and shape. Column A contains labels, and doesn’t affect the robot, while Column B contains data. The first row (cell B1) is used to define whether the robot is a circle (0) or rectangle (1). The second row (cell B2)

defines the robot diameter in inches if the robot is circular, or the x-dimension in inches if the robot is rectangular. The third row (cell B3) defines the robot

y-dimension in inches if the robot is rectangular, and has no effect if it is circular.
The function import bot.m reads robot.csv and converts it to a shape composed of perimeter points as defined by the file. The first column de-

9

fines the x-coordinates, and the second column defines the y-coordinates, defined in a clockwise direction. The first point and last point must be the same to ensure that the shape is closed. If it is desired to use a custom perimeter shape instead of the standard circle or rectangle, the output of import bot.m can be replaced with a list of x-y points in the same format. The robot centroid for purposes of movement and sensor position definition is assumed to be at the origin (0,0).

### 4.3 Sensors

Relevant files

1. sensors.csv - sensor loadout definition file
2. import sensor.m - MATLAB function to import the sensors

The file sensors.csv in the config folder is used to define the robot’s sensors, include the type, location, and orientation of each. Figure 1 shows the layout of an example file, with each row representing a different sensor. Each column is used to define a particular characteristic of the sensor.

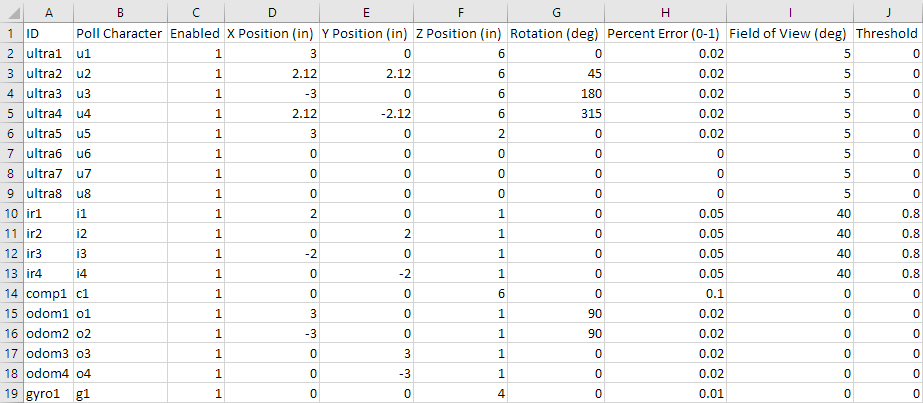
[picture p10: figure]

Figure 1: Sample sensor configuration .csv file

10

### 4.3.1 Column A - ID

Column A is the sensor ID. This defines the type of sensor. Five sensor types are supported, defined as a text string unique to the sensor followed by a number. The below tags MUST be used in this column, they can not be replaced with custom tags. Up to ten sensors of each type can be used.

1. ultra - Ultrasonic sensor
2. ir - Downward facing infrared sensor (line-following sensor)
3. comp - Compass
4. odom - Wheel odometer
5. gyro - Gyroscope (rotation only)

### 4.3.2 Column B - Poll Character

The Poll Character is a two-character code that is used to command the simulator (or robot if communicating via Bluetooth serial). These can be

customized by the user to be anything in the format ”letter”-”number”. The letter should be consistent among sensors, i.e. if using ”u1” for one ultrasonic sensor, you should use ”u2” for the second, ”u3” for the third, etc. If using ”s1”, you should use ”s2”, ”s3”, etc.

### 4.3.3 Column C - Enabled

This column should be either 1 or 0, indicating whether the sensor is enabled or disabled, respectively. This column allows for sensors to be temporarily disabled without deleting them from the file.

11

### 4.3.4 Column D-F - X-Position, Y-Position, Z-Position

These three columns define the position of a sensor, in inches from the center (X & Y) and base (Z). For ultrasonic sensors, the Z-position determines if

the sensor can detect a block. For IR sensors, Z-position determines the area visible to the sensor. For compasses and gyroscopes, these numbers must be entered but do not factor into calculations. For information on the local and global reference frames for the robot, see Section 5.3.

### 4.3.5 Column G - Rotation

This column denotes the rotation of a sensor relative to the body of the robot, in degrees from the X-positive direction. For compasses, gyroscopes, and IR sensors, these numbers must be entered but do not factor into calculations. For information on the local and global reference frames for the robot, see Section 5.3.

### 4.3.6 Column H - Percent Error

This column indicates the normally distributed random error added to measurements by the simulator for the sensor. This is defined on a scale from 0 to 100%, where 1% error is entered as 0.01. Equation 1 is used to calculate the

error. Vi

is the true value, Rn is a random number selected from a weighted normal distribution centered about 0, and P is the percent error value for the sensor.

V = Vi ∗ (1 + Rn ∗ P) | (1)

### 4.3.7 Column I - Field of View

This column represents the field of view for sensors where it is relevant, in degrees (full-angle). This is only relevant for ultrasonic and IR sensors. For

example, a field of view of 5 degrees means that a cone is visible to the sensor

12 from +2.5° to -2.5° off the center axis. For all other sensors, this value must

be entered but is not used in calculations.

### 4.3.8 Column J - Threshold

This value is only used by IR sensors, for all other sensors it must be entered but is not used in calculations. This column represents the percentage of the field of view of an IR sensor that must be black before it registers as black. This is entered as a value from 0 to 1, where 0.8 corresponds to 80%.

### 4.4 Drive

Relevant files

1. drive.csv - drive definition file
2. import drive.m - MATLAB function to import the drive mechanism and commands

Similar to sensors.csv, the drive config file is used to import information about the drive mechanism of the robot to be simulated or tested. An example drive configuration is shown in Figure 2 for a robot with 4x Omniwheel drive, capable of moving in each axis and and rotating independently.

Figure 2: Sample drive configuration .csv file

13

### 4.4.1 Column A - ID

Column A is the direction ID. Five drive directions are supported, defined as a text string unique to the direction followed by a number. The below tags MUST be used in this column, they can not be replaced with custom tags. Unlike for the sensors, each of these can only be used once.

1. up - Upward movement (Y+)
2. down - Downward movement (Y-)
3. left - Left movement (X-)
4. right - Right movement (X+)
5. rot - Rotational movement

For information on the local and global reference frames for the robot, see Section 5.3. Typically, right would be defined as ”forward” but it is up to you to determine and configure this for your design.

### 4.4.2 Column B - Poll Character

The Poll Character is a two-character code that is used to command the simulator (or robot if communicating via Bluetooth serial). These can be

customized by the user to be anything in the format ”letter”-”number”. The letter should be unique for each direction, and MUST NOT overlap with any of the sensor poll characters.

### 4.4.3 Column C - Enabled

This column should be either 1 or 0, indicating whether the drive direction is enabled or disabled, respectively. For instance, if a robot is not using omni-wheels or a similar drive mechanism, the left & right directions can be disabled to accurately represent the drive mechanism.

14

### 4.4.4 Column D-F - Y, X-Axis Error & Rotation Error

These columns, similar to the Percent Error column in the sensors.csv, define the normalized random component of error in either a direction or rotation axis when the robot is commanded to drive or rotate in a direction. This is similar to the process described in Section 4.3.6. Equations 2, 3, and 4 illustrate exactly how the movement is calculated, where the terms are the same as in Equation 1 with subscripts x and y indicating X- and Y- axis values.

Vx = (Vxi + Vyi + Vri) ∗ Rn ∗ Px + Vxi | (2)
Vy = (Vxi + Vyi + Vri) ∗ Rn ∗ Py + Vyi | (3)
Vr = (Vxi + Vyi + Vri) ∗ Rn ∗ Pr + Vri | (4)

### 4.4.5 Column G-I - Y, X-Axis Bias & Rotation Bias

These columns define the bias, or persistent error, for each of the drive commands. They work similarly to the normalized error in Section 4.4.4. For the Y-axis and X-axis bias, they are defined such that for each inch commanded, the value in the bias column is also moved in the appropriate direction. For example, If a robot has an X-bias of 0.1 in the up direction, if it is commanded to move right 2 inches, it will move right 1 inch and drift upward 0.2 inches, plus any error calculated as in Section 4.4.4. Rotation bias is calculated similarly, except inches moved is replaced with degrees rotated. Similar to the previous example, if a value of -3 is listed in the Rotation Bias column for the right direction, if the robot is commanded to move 2 inches to the right, it will, at the same time, rotate -6 degrees while executing the movement. For the rotation movement command, the biases act similarly, where each degree of rotation commanded translates to either an inch of movement bias or degree of rotation bias. The scale factors must be set appropriately in order to ensure representative biases in the drive. There is a way to randomize

15 these biases for each simulation run within the simulator code, if a user does not wish to hard code values into the config file. If randomized biases are used, they will overwrite the values entered in these columns.

16

## 5 Simulator User Guide

This section is a user guide intended for anyone who needs to use the simulator rather than make changes to its code. Prior to reading this section, readers should read Section 4 to ensure they understand how to properly set up the simulator.

### 5.1 Matlab setup

Ensure that Matlab version 2020a or newer is installed. The simulator may work with older versions, but keep in mind that it has NOT been tested with them for compatibility. Download the SimMeR code from GitHub, and unpack it to a location on your computer from which it can be run.
To run the simulator, you must run the script Main.m from the main folder. All functions that are needed are contained in the main folder, you should not need to add any additional paths for functionality. Ensure configuration .csv files are located in a folder called config within the main folder. This is the default location.
The simulator uses TCP to communicate with a control algorithm. This algorithm can be written in Matlab, Python, or another language that supports sending strings and double-precision floating point numbers over TCP packets. It has only been tested with Matlab, so please be aware if you are trying to use another language that some debugging may be necessary. TCP packets are exchanged over the localhost, and so an internet connection is not required as long as SimMeR and the control algorithm are running on the same computer. Your firewall may block Matlab’s access to localhost by default. If you can’t get your control algorithm software to connect to SimMeR, you may have to grant Matlab access (the popup shown in Figure 3 shows Windows firewall blocking it). SimMeR uses port 9000 and 9001 to

receive commands and send replies, by default. These can be changed by editing the values passed to tcp setup.m.

17

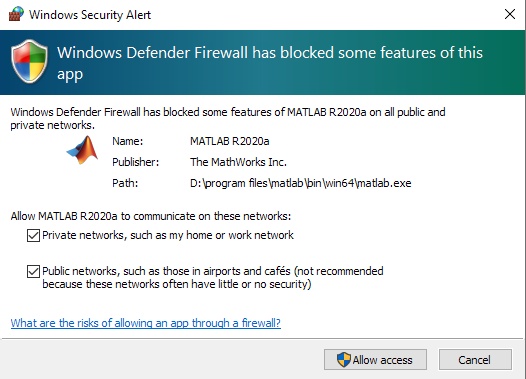
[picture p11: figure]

Figure 3: Windows firewall blocking Matlab TCP access.

### 5.2 SimMeR Display Window

SimMeR displays a visualization of the robot traversing through the maze. This section describes the plot display and the objects on it.
Figure 4 shows the display window. The x- and y-axis values represent inches from the origin, the bottom-left of the window. The black rectangle surrounding the maze is the outer wall, while the filled-in black boxes represent additional internal walls. Each of the solid walls are 1 foot by 1 foot in size. Light gray and white squares represent the checkerboard pattern of the maze. Each of these squares is 3 inches by 3 inches.
The block that the robot must pick up is denoted by the yellow translucent square on the maze. In this instance of the simulator, the robot has been defined as a circle, but it can be configured as a rectangle or another shape. In any case, the robot appears as a green translucent polygon. The +X direction on the robot is indicated by a black asterisk. Movement of the robot is displayed as a trail of red asterisks, which updates each time the robot moves.

18

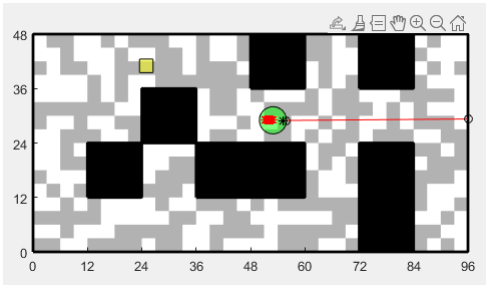
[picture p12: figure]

Figure 4: SimMeR main display window.

The red line extending from the front of the robot to the wall in Figure 4 is the ”ray” that represents the distance an ultrasonic sensor is measuring. In Figure 5, the closeup of an IR sensor reading is displayed. The blue outer circle is the area of the ground an IR sensor can ”see” based on its defined field-of-view (FOV) angle and z-position height above the surface. The red

circles show each of the test points within the FOV, and black X’s indicate the test points where the checkerboard pattern is black.

### 5.3 Reference Frames

In SimMeR, all reference frames are designated in a mathematically consistent manner. Looking at the display window shown in 4, the global coordinate system is defined as 0° (X+) to the right, +90° (Y+) in the upward direction, +180° (X-) to the left, and +270° (Y-) in the downward direction.

Note that whenever a rotation must be specified, +/- degrees can both be

used, as can values greater than 360 degrees. Values greater than 360 degrees or less than 0 degrees may also be output in the case of some sensors, such

19

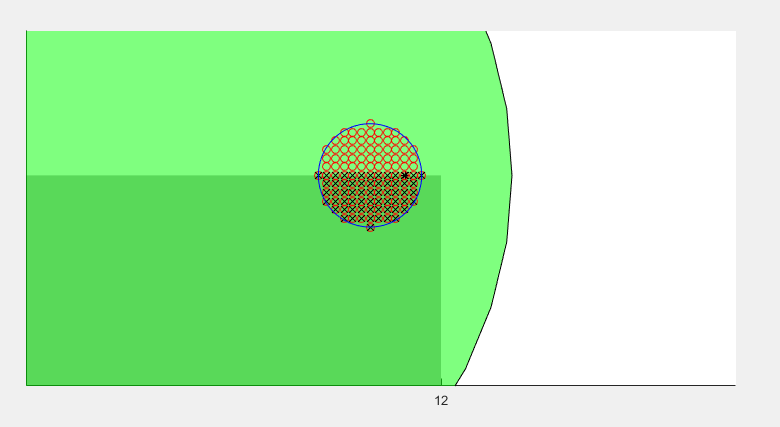
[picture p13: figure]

Figure 5: The visualization of an IR sensor reading (zoomed in).

as gyroscopes.
In the robot’s local coordinate system, the robot displayed on the plot will always have a small black asterisk on the side defined as X+ (0°).

### 5.4 Setup Values and Flags

This section details a number of user-editable flags and constants that appear at the beginning of the Main.m script. Each of these can be set by the user, and they are the only values that should be edited in a typical configuration.

### 5.4.1 Setup Values

- bot center - starting location of the robot centroid [x,y] in inches.
- bot rot - starting rotation of the robot, in degrees.
- block center - starting location of the block centroid [x,y] in inches.
- blocksize - side length of the block, in inches.

20

- num segments - the number of segments SimMeR breaks each move-

ment command down into. More segments will generally equate to more representative movement and collision detection, at the cost of computation time. Set to 10 by default.

- strength - if random drive bias is enabled, determines the ”strength”

of the bias, with higher numbers resulting in more bias. Should be defined as a two-element row vector. The first element determines bias strength of directional movements, the second determines rotation bias strength. Set to [0.05, 1] by default.

- step time - Time in seconds to pause between each command executed

by the simulator. Primarily used for debugging, if pauses are needed it is better to implement them in the user algorithm if possible. Set to 0 by default.

### 5.4.2 Flags

- randerror - use either true random number generation (1) or consistent

random number generation (0). Set to 1 by default.

- randbias - use a randomized, normally distributed set of drive biases.

Set to 1 by default.

- sim - use the simulator (1) or connect to robot via Bluetooth (0). Set

to 1 by default, as Bluetooth is not yet implemented.

- plot robot - Enable the main display window (1) or disable it (0). Set

to 1 by default.

- plot sense - Enable the plotting of sensor interactions with the maze,

such as IR and ultrasonic sensors (1), or disable it (0). Set to 1 by

default.

21

### 5.5 Communicating with SimMeR

Relevant Files

1. tcp setup.m - creates TCP server/client objects.
2. tcpclient write.m - writes string data to a tcp socket, and waits for a response. Outputs the response as an 8 byte double precision floating point number.
3. tcpclient write.m - reads string data from a tcp socket.

As mentioned in Section 5.1, SimMeR uses TCP sockets to send and receive data between itself and the control algorithm. This section describes that data exchange in more detail.
If a user is programming their algorithm in MATLAB, communication is simple. In the algorithm script at the beginning before the main loop, the following lines of code need to be inserted.

[s_cmd, s_rply] = tcp_setup();

fopen(s_cmd);

fopen(s_rply);

The first line creates two TCP client sockets, s cmd and s rply, on port 9000 and port 9001, respectively. These can be modified by adding the input arguments role, port1, and port2, where role is ’client’ and port1 and port2 are ports of your choosing. Keep in mind that if these values are changed, the values in the simulator file Main.m must also be updated accordingly. The second and third lines open the two ports. Note that this must be done after the TCP server is set up and its ports opened by SimMeR, therefore you must run SimMeR and allow it to reach the stage where it displays ’Simulator initialized... waiting for connection from client’ before running the control algorithm.
To send data to SimMeR, use the following command in Matlab:

22 data = tcpclient_write(cmdstring, s_cmd, s_rply);

This function sends data over the socket s cmd, which should be a string of the format [CC-V] (not including the brackets), and waits for a response

on socket s rply, which should be an eight byte double precision floating point number.

### 5.5.1 Data Formats

The first half (CC) MUST be a TWO character command code specified in

one of either the sensors.csv or drive.csv files. If the command code corresponds to a drive direction or rotation, the second half (V) should correspond to the movement value, using as many characters as needed. All commands MUST end in a newline character (newline in MATLAB or ’\10’ in many other languages, new in version 0.2). For drive directions, this is distance

in inches, for rotations, rotation in degrees. The two halves should always be separated by a hyphen character. To represent negative numbers, use a hyphen before the number, as normal. To represent a number with a decimal value, use a period, again as normal. Note that an easy way to generate strings in the correct format is using the built-in Matlab function num2str().

If the command code corresponds to a sensor, the hyphen and second half (V) can be omitted. A few examples are illustrated below, note that the

newline character is not shown but it MUST be included at the end of each of these example strings for the simulator to work correctly. Single quotes (’)

represent information in string format. In this example, ’u1’ is the command code for an ultrasonic sensor, ’r1’ is the command code for a rotation, and ’d1’ is the command code for movement in the +X direction (using the robot local coordinate reference frame).

- ’u1’ - polls the ultrasonic sensor. Distance is returned as an eight byte

double.

23

- ’u1-10’ - also polls the ultrasonic sensor. The trailing ’-10’ is ignored

since it is not relevant.

- ’d1-3’ - tells the robot to move 3 inches in the +X direction
- ’d1-2.4’ - tells the robot to move 2.4 inches in the +X direction
- ’r1-45’ - tells the robot to rotate +45 degrees (counter-clockwise)
- ’r1–45’ - tells the robot to rotate -45 degrees (clockwise, note that there

are two hyphens in this code)

Sensor reading commands will always return a single eight byte double as their reply. Movement and rotation commands will return Infinity once completed. If a command code can’t be matched to one defined in sensors.csv or drive.csv, NaN will be returned.

### 5.6 Running SimMeR

To run a simulation, two programs are required. SimMeR must be run in Matlab, and the control algorithm must be run (if written in Matlab, it must be run in a second instance of Matlab). The order that programs must be

run in is shown below. For this example, the sample obstacle avoidance algorithm test.m is used.

1. Open an instance of Matlab in which to run SimMeR (Matlab-1).
2. Open a second instance of Matlab in which the control algorithm will be run (Matlab-2).
3. In Matlab-1, navigate to the correct folder (or add it to the Matlab path) and open Main.m.
4. Ensure that the config files (Section 4) and Setup variables and Flags in Main.m (Section 5.4) are configured correctly.

24

5. In Matlab-2, navigate to the correct folder (or add it to the Matlab path) and open test.m.
6. In Matlab-1, run Main.m. Wait for it to display ’Simulator initialized... waiting for connection from client’ in the Command Window.
7. In Matlab-2, run test.m.

25

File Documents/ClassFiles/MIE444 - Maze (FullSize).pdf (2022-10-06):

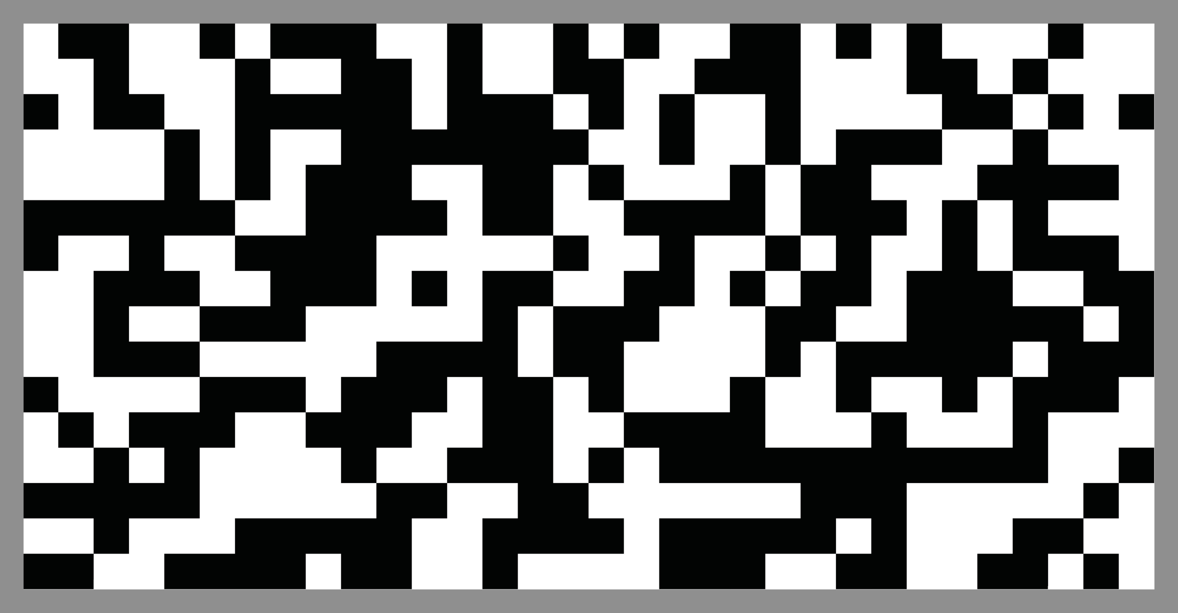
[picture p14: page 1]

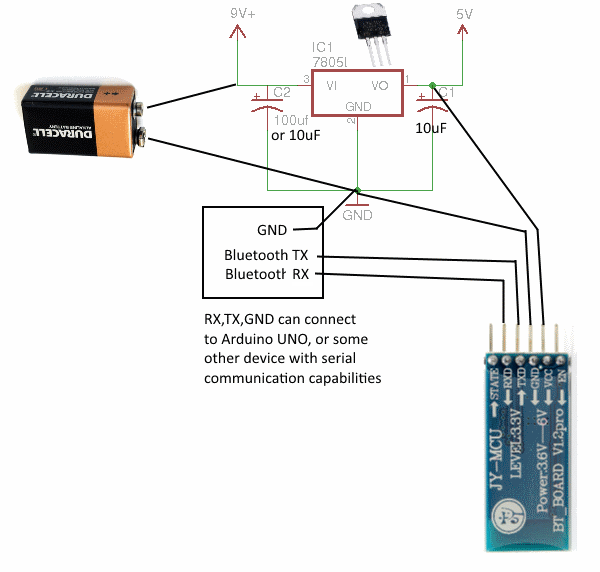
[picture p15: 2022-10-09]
Documents/SampleCodes/Bluetooth/SmallBluetoothBoards.gif

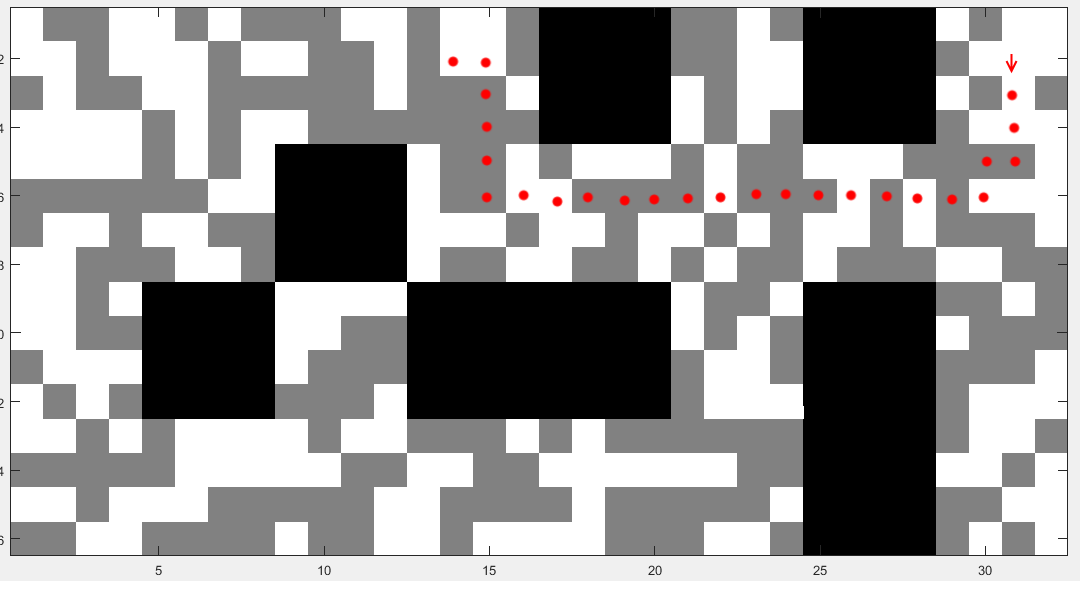
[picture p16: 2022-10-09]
Documents/SampleCodes/Localization/HistogramLocalization2D_IR/sample_movement.png

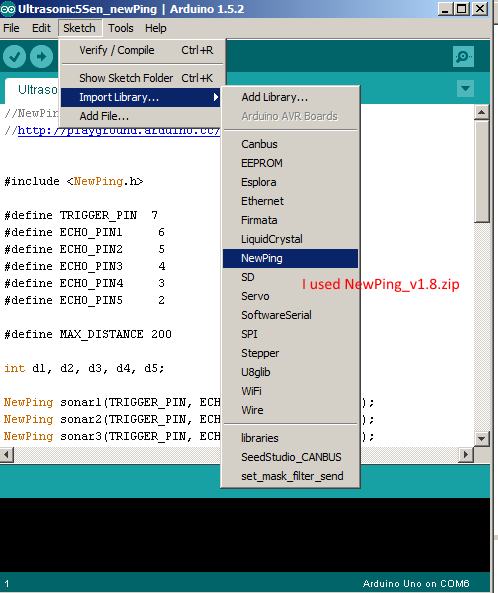
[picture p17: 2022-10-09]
Documents/SampleCodes/Ultrasonic/Add NewPing to Arduino Library.png

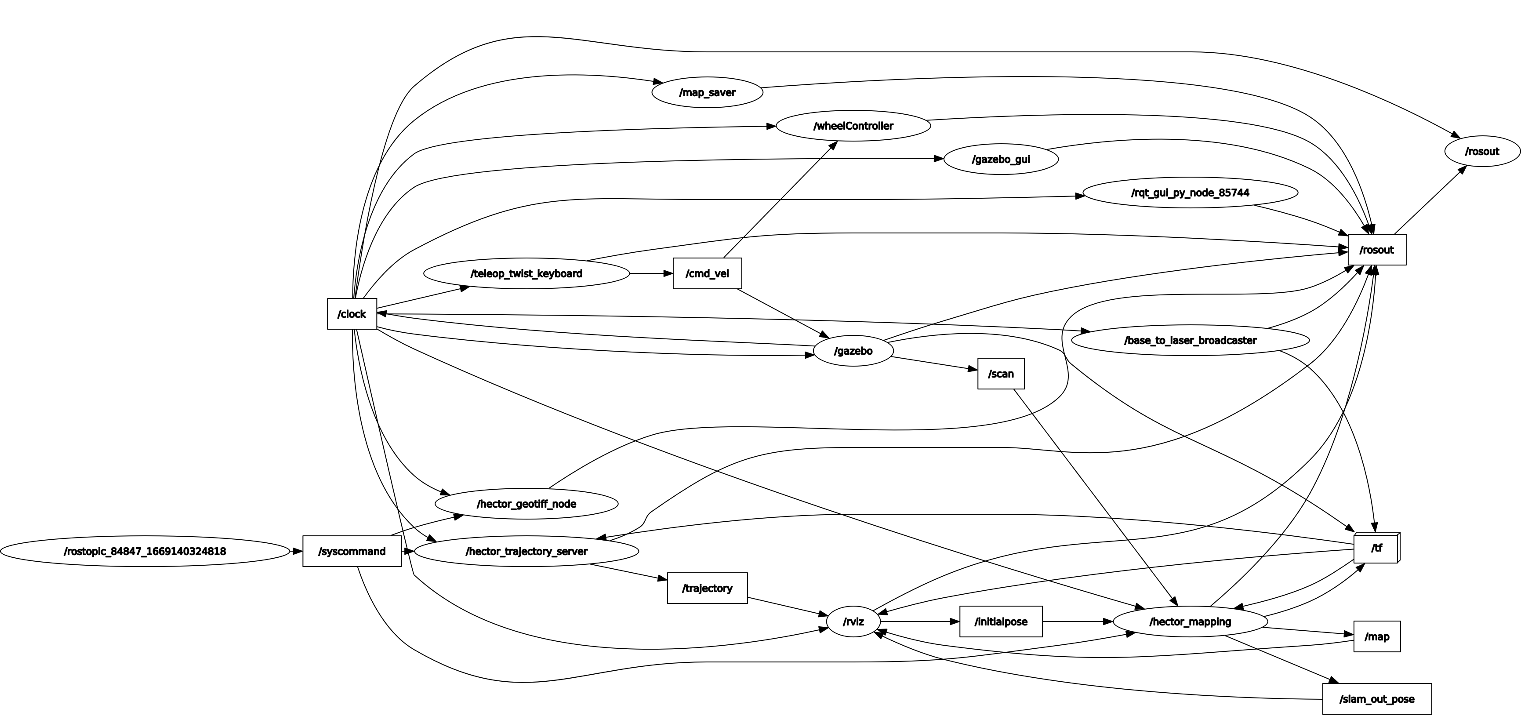
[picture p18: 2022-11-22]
Documents/Hector_sim_rqtgraph.png

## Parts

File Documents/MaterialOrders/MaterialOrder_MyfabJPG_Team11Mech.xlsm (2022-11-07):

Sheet: OrdersNew
Mechatronics List |  |  |  |  |  |  | Materials List |  |  |  |  | Hardware List
Filename | Category | Spec sheet | RentalCost | Rental | OutOfStock | IDMECHATRONICS | Filename | UnitSize | Cost | OutOfStock2 | IDMaterials | Filename | Category | Specs | Cost | OutOfStock2 | IDSpecialtyHardware
22awg solid black 1 ft | Connect | http://www.cnctech.us/pdfs/UL%2010982%20AWG%2022.pdf http://www.cnctech.us/pdfs/UL%2010982%20AWG%2022.pdf | 0.33 | Final Sale | (blank) | 9 MECHATRONICS | Birch Ply 1/8" | 18"x24" | 2.61 | (blank) | 3 MATERIALS | Hex nut M3 pitch 0.5 | Nuts | (blank) | 0.08 | (blank) | 23 HARDWARE
22awg solid blue 1 ft | Connect | https://www.alphawire.com/products/wire/hook-up-wire/premium/3051_1/ https://www.alphawire.com/products/wire/hook-up-wire/premium/3051_1/ | 0.33 | Final Sale | (blank) | 10 MECHATRONICS |  |  |  |  |  | M3 Locknut | Nuts | M3 | 0.09 | (blank) | 92 HARDWARE
22awg solid red 1ft | Connect | (blank) | 0.33 | Final Sale | (blank) | 60 MECHATRONICS |  |  |  |  |  | M3 pitch 0.50- 10mm | Machine screws | 10 mm | 0.12 | (blank) | 15 HARDWARE
22awg solid violet 1ft | Connect | (blank) | 0.33 | Final Sale | (blank) | 43 MECHATRONICS |  |  |  |  |  | M3 pitch 0.50- 12mm | Machine screws | 12 mm | 0.07 | (blank) | 16 HARDWARE
22awg solid yellow 1ft | Connect | (blank) | 0.33 | Final Sale | (blank) | 44 MECHATRONICS |  |  |  |  |  | M3 pitch 0.50- 25mm | Machine screws | 25 mm | 0.12 | (blank) | 18 HARDWARE
22awg solig green 1 ft | Connect | (blank) | 0.33 | Final Sale | (blank) | 59 MECHATRONICS |  |  |  |  |  | M3 pitch 0.50- 35mm | Machine screws | 35 mm | 0.14 | (blank) | 19 HARDWARE
3-Position Breakout | Connect | https://www.mouser.ca/datasheet/2/595/BB-TERM3-471790.pdf https://www.mouser.ca/datasheet/2/595/BB-TERM3-471790.pdf | 1.18 | Rental | (blank) | 64 MECHATRONICS |  |  |  |  |  | M3 pitch 0.50- 5mm | Machine screws | 5mm | 0.09 | - | 12 HARDWARE
AC-DC power supply 12V 5A | Power | (blank) | 4.32 | Rental | - | 1 MECHATRONICS |  |  |  |  |  | M3 Washers | Washers | M3 | 0.02 | (blank) | 48 HARDWARE
Dupont Connector 2 pin | Connect | (blank) | 0.07 | Final Sale | (blank) | 78 MECHATRONICS
Dupont Connector 3 pin | Connect | (blank) | 0.07 | Final Sale | (blank) | 79 MECHATRONICS
Dupont Connector 5 pin | Connect | (blank) | 0.07 | Final Sale | (blank) | 80 MECHATRONICS
Dupont Connector Reed F (10 units) | Connect | (blank) | 0.2 | Final Sale | (blank) | 88 MECHATRONICS
Dupont Connector Reed M (10 units) | Connect | (blank) | 0.42 | Final Sale | (blank) | 89 MECHATRONICS
F-M Stackable Header 4 pin | Connect | (blank) | 0.44 | Final Sale | (blank) | 86 MECHATRONICS
Hex Standoff M3 8.00mm F-M | Hardware | https://www.we-online.com/katalog/datasheet/971100354.pdf https://www.we-online.com/katalog/datasheet/971100354.pdf | 0.066 | Rental | (blank) | 72 MECHATRONICS
Hex Standoff M3 50mm M-F | Hardware | https://www.we-online.com/katalog/datasheet/971500324.pdf https://www.we-online.com/katalog/datasheet/971500324.pdf | 0.2 | Rental | (blank) | 68 MECHATRONICS
LED | Component | https://learn.adafruit.com/all-about-leds/the-led-datasheet https://learn.adafruit.com/all-about-leds/the-led-datasheet | 0.35 | Final Sale | (blank) | 40 MECHATRONICS
PCB receptacle board to board 4pos 1 ros | Connect | https://www.farnell.com/datasheets/185042.pdf https://www.farnell.com/datasheets/185042.pdf | 1.18 | Final Sale | - | 12 MECHATRONICS
Pin header 40 contacts | Connect | https://www.we-online.com/katalog/datasheet/61304011121.pdf https://www.we-online.com/katalog/datasheet/61304011121.pdf | 1.21 | Final Sale | (blank) | 11 MECHATRONICS
Solder Breadboard (10row x 5column) | Connect | https://www.mouser.ca/datasheet/2/73/SBB1005_1-2488414.pdf https://www.mouser.ca/datasheet/2/73/SBB1005_1-2488414.pdf | 2.72 | Final Sale | (blank) | 6 MECHATRONICS
Solder Breadboard (16row x 5column) | Connect | https://www.mouser.ca/datasheet/2/73/SBB1605_1-2488593.pdf https://www.mouser.ca/datasheet/2/73/SBB1605_1-2488593.pdf | 4.61 | Final Sale | (blank) | 7 MECHATRONICS
USB to Micro USB cable | Connect | (blank) | 0.466 | Rental | (blank) | 8 MECHATRONICS
330 ohms resistor | Component | https://www.seielect.com/catalog/sei-cf_cfm.pdf https://www.seielect.com/catalog/sei-cf_cfm.pdf | 0.01 | Final Sale | (blank) | 120 MECHATRONICS
1 Kohms resistor | Component | https://www.seielect.com/catalog/sei-cf_cfm.pdf https://www.seielect.com/catalog/sei-cf_cfm.pdf | 0.01 | Final Sale | (blank) | 121 MECHATRONICS
Hex Standoff M3 10.00mm F-M | Hardware | https://www.we-online.com/katalog/datasheet/971100354.pdf https://www.we-online.com/katalog/datasheet/971100354.pdf | 0.064 | Rental | (blank) | 71 MECHATRONICS
Raspberry Pi 4 4GB RAM | External | (blank) | 0 | Final Sale | (blank) | 203 MECHATRONICS
USB Micro-B power supply for RPI | External | (blank) | 0 | Final Sale | (blank) | 205 MECHATRONICS

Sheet: PurchaseOrder
MYFab Purchase order form
UtorID | 1005469217 |  | Total (CAD) |  | $21.83
Description | Specs/Category | Quantity | Unit $ | Out of Stock | ID | Terms | Subtotal
Hex Standoff M3 8.00mm F-M | Hardware | 36 | 0.066 | (blank) | 72 MECHATRONICS | Rental | 2.376
Hex Standoff M3 50mm M-F | Hardware | 8 | 0.2 | (blank) | 68 MECHATRONICS | Rental | 1.6
LED | Component | 1 | 0.35 | (blank) | 40 MECHATRONICS | Final Sale | 0.35
Hex nut M3 pitch 0.5 | Nuts | 10 | 0.08 | (blank) | 23 HARDWARE |  | 0.8
M3 Locknut | Nuts | 75 | 0.09 | (blank) | 92 HARDWARE |  | 6.75
M3 pitch 0.50- 12mm | Machine screws | 15 | 0.07 | (blank) | 16 HARDWARE |  | 1.05
M3 pitch 0.50- 25mm | Machine screws | 25 | 0.12 | (blank) | 18 HARDWARE |  | 3
M3 pitch 0.50- 35mm | Machine screws | 15 | 0.14 | (blank) | 19 HARDWARE |  | 2.1
M3 pitch 0.50- 5mm | Machine screws | 40 | 0.09 | - | 12 HARDWARE |  | 3.6
M3 Washers | Washers | 10 | 0.02 | (blank) | 48 HARDWARE |  | 0.2
Notes:
Only modify the column Quantity
When done Print and submit the pdf
If met with error "The specified file is read only", close the purchase order that is open in the pdf viewer

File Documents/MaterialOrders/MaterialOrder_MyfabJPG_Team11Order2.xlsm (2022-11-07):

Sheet: OrdersNew
Mechatronics List |  |  |  |  |  |  | Materials List |  |  |  |  | Hardware List
Filename | Category | Spec sheet | RentalCost | Rental | OutOfStock | IDMECHATRONICS | Filename | UnitSize | Cost | OutOfStock2 | IDMaterials | Filename | Category | Specs | Cost | OutOfStock2 | IDSpecialtyHardware
22awg solid black 1 ft | Connect | http://www.cnctech.us/pdfs/UL%2010982%20AWG%2022.pdf http://www.cnctech.us/pdfs/UL%2010982%20AWG%2022.pdf | 0.33 | Final Sale | (blank) | 9 MECHATRONICS | Birch Ply 1/8" | 18"x24" | 2.61 | (blank) | 3 MATERIALS | Hex nut M3 pitch 0.5 | Nuts | (blank) | 0.08 | (blank) | 23 HARDWARE
22awg solid blue 1 ft | Connect | https://www.alphawire.com/products/wire/hook-up-wire/premium/3051_1/ https://www.alphawire.com/products/wire/hook-up-wire/premium/3051_1/ | 0.33 | Final Sale | (blank) | 10 MECHATRONICS |  |  |  |  |  | M3 Locknut | Nuts | M3 | 0.09 | (blank) | 92 HARDWARE
22awg solid red 1ft | Connect | (blank) | 0.33 | Final Sale | (blank) | 60 MECHATRONICS |  |  |  |  |  | M3 pitch 0.50- 10mm | Machine screws | 10 mm | 0.12 | (blank) | 15 HARDWARE
22awg solid violet 1ft | Connect | (blank) | 0.33 | Final Sale | (blank) | 43 MECHATRONICS |  |  |  |  |  | M3 pitch 0.50- 12mm | Machine screws | 12 mm | 0.07 | (blank) | 16 HARDWARE
22awg solid yellow 1ft | Connect | (blank) | 0.33 | Final Sale | (blank) | 44 MECHATRONICS |  |  |  |  |  | M3 pitch 0.50- 25mm | Machine screws | 25 mm | 0.12 | (blank) | 18 HARDWARE
22awg solig green 1 ft | Connect | (blank) | 0.33 | Final Sale | (blank) | 59 MECHATRONICS |  |  |  |  |  | M3 pitch 0.50- 35mm | Machine screws | 35 mm | 0.14 | (blank) | 19 HARDWARE
3-Position Breakout | Connect | https://www.mouser.ca/datasheet/2/595/BB-TERM3-471790.pdf https://www.mouser.ca/datasheet/2/595/BB-TERM3-471790.pdf | 1.18 | Rental | (blank) | 64 MECHATRONICS |  |  |  |  |  | M3 pitch 0.50- 5mm | Machine screws | 5mm | 0.09 | - | 12 HARDWARE
AC-DC power supply 12V 5A | Power | (blank) | 4.32 | Rental | - | 1 MECHATRONICS |  |  |  |  |  | M3 Washers | Washers | M3 | 0.02 | (blank) | 48 HARDWARE
Dupont Connector 2 pin | Connect | (blank) | 0.07 | Final Sale | (blank) | 78 MECHATRONICS
Dupont Connector 3 pin | Connect | (blank) | 0.07 | Final Sale | (blank) | 79 MECHATRONICS
Dupont Connector 5 pin | Connect | (blank) | 0.07 | Final Sale | (blank) | 80 MECHATRONICS
Dupont Connector Reed F (10 units) | Connect | (blank) | 0.2 | Final Sale | (blank) | 88 MECHATRONICS
Dupont Connector Reed M (10 units) | Connect | (blank) | 0.42 | Final Sale | (blank) | 89 MECHATRONICS
F-M Stackable Header 4 pin | Connect | (blank) | 0.44 | Final Sale | (blank) | 86 MECHATRONICS
Hex Standoff M3 8.00mm F-M | Hardware | https://www.we-online.com/katalog/datasheet/971100354.pdf https://www.we-online.com/katalog/datasheet/971100354.pdf | 0.066 | Rental | (blank) | 72 MECHATRONICS
Hex Standoff M3 50mm M-F | Hardware | https://www.we-online.com/katalog/datasheet/971500324.pdf https://www.we-online.com/katalog/datasheet/971500324.pdf | 0.2 | Rental | (blank) | 68 MECHATRONICS
LED | Component | https://learn.adafruit.com/all-about-leds/the-led-datasheet https://learn.adafruit.com/all-about-leds/the-led-datasheet | 0.35 | Final Sale | (blank) | 40 MECHATRONICS
PCB receptacle board to board 4pos 1 ros | Connect | https://www.farnell.com/datasheets/185042.pdf https://www.farnell.com/datasheets/185042.pdf | 1.18 | Final Sale | - | 12 MECHATRONICS
Pin header 40 contacts | Connect | https://www.we-online.com/katalog/datasheet/61304011121.pdf https://www.we-online.com/katalog/datasheet/61304011121.pdf | 1.21 | Final Sale | (blank) | 11 MECHATRONICS
Solder Breadboard (10row x 5column) | Connect | https://www.mouser.ca/datasheet/2/73/SBB1005_1-2488414.pdf https://www.mouser.ca/datasheet/2/73/SBB1005_1-2488414.pdf | 2.72 | Final Sale | (blank) | 6 MECHATRONICS
Solder Breadboard (16row x 5column) | Connect | https://www.mouser.ca/datasheet/2/73/SBB1605_1-2488593.pdf https://www.mouser.ca/datasheet/2/73/SBB1605_1-2488593.pdf | 4.61 | Final Sale | (blank) | 7 MECHATRONICS
USB to Micro USB cable | Connect | (blank) | 0.466 | Rental | (blank) | 8 MECHATRONICS
330 ohms resistor | Component | https://www.seielect.com/catalog/sei-cf_cfm.pdf https://www.seielect.com/catalog/sei-cf_cfm.pdf | 0.01 | Final Sale | (blank) | 120 MECHATRONICS
1 Kohms resistor | Component | https://www.seielect.com/catalog/sei-cf_cfm.pdf https://www.seielect.com/catalog/sei-cf_cfm.pdf | 0.01 | Final Sale | (blank) | 121 MECHATRONICS
Hex Standoff M3 10.00mm F-M | Hardware | https://www.we-online.com/katalog/datasheet/971100354.pdf https://www.we-online.com/katalog/datasheet/971100354.pdf | 0.064 | Rental | (blank) | 71 MECHATRONICS
Raspberry Pi 4 4GB RAM | External | (blank) | 0 | Final Sale | (blank) | 203 MECHATRONICS
USB Micro-B power supply for RPI | External | (blank) | 0 | Final Sale | (blank) | 205 MECHATRONICS

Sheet: PurchaseOrder
MYFab Purchase order form
UtorID | 1005469217 |  | Total (CAD) |  | $46.76
Description | Specs/Category | Quantity | Unit $ | Out of Stock | ID | Terms | Subtotal
22awg solid black 1 ft | Connect | 4 | 0.33 | (blank) | 9 MECHATRONICS | Final Sale | 1.32
22awg solid blue 1 ft | Connect | 2 | 0.33 | (blank) | 10 MECHATRONICS | Final Sale | 0.66
22awg solid red 1ft | Connect | 4 | 0.33 | (blank) | 60 MECHATRONICS | Final Sale | 1.32
22awg solid violet 1ft | Connect | 2 | 0.33 | (blank) | 43 MECHATRONICS | Final Sale | 0.66
22awg solid yellow 1ft | Connect | 2 | 0.33 | (blank) | 44 MECHATRONICS | Final Sale | 0.66
22awg solig green 1 ft | Connect | 2 | 0.33 | (blank) | 59 MECHATRONICS | Final Sale | 0.66
3-Position Breakout | Connect | 2 | 1.18 | (blank) | 64 MECHATRONICS | Rental | 2.36
Dupont Connector 2 pin | Connect | 2 | 0.07 | (blank) | 78 MECHATRONICS | Final Sale | 0.14
Dupont Connector 3 pin | Connect | 3 | 0.07 | (blank) | 79 MECHATRONICS | Final Sale | 0.21
Dupont Connector 5 pin | Connect | 5 | 0.07 | (blank) | 80 MECHATRONICS | Final Sale | 0.35
Dupont Connector Reed F (10 units) | Connect | 1 | 0.2 | (blank) | 88 MECHATRONICS | Final Sale | 0.2
Dupont Connector Reed M (10 units) | Connect | 1 | 0.42 | (blank) | 89 MECHATRONICS | Final Sale | 0.42
F-M Stackable Header 4 pin | Connect | 10 | 0.44 | (blank) | 86 MECHATRONICS | Final Sale | 4.4
Hex Standoff M3 8.00mm F-M | Hardware | 36 | 0.066 | (blank) | 72 MECHATRONICS | Rental | 2.376
Hex Standoff M3 50mm M-F | Hardware | 8 | 0.2 | (blank) | 68 MECHATRONICS | Rental | 1.6
LED | Component | 1 | 0.35 | (blank) | 40 MECHATRONICS | Final Sale | 0.35
PCB receptacle board to board 4pos 1 ros | Connect | 1 | 1.18 | - | 12 MECHATRONICS | Final Sale | 1.18
Pin header 40 contacts | Connect | 1 | 1.21 | (blank) | 11 MECHATRONICS | Final Sale | 1.21
Solder Breadboard (10row x 5column) | Connect | 1 | 2.72 | (blank) | 6 MECHATRONICS | Final Sale | 2.72
Solder Breadboard (16row x 5column) | Connect | 1 | 4.61 | (blank) | 7 MECHATRONICS | Final Sale | 4.61
USB to Micro USB cable | Connect | 1 | 0.466 | (blank) | 8 MECHATRONICS | Rental | 0.466
330 ohms resistor | Component | 2 | 0.01 | (blank) | 120 MECHATRONICS | Final Sale | 0.02
1 Kohms resistor | Component | 2 | 0.01 | (blank) | 121 MECHATRONICS | Final Sale | 0.02
Hex Standoff M3 10.00mm F-M | Hardware | 21 | 0.064 | (blank) | 71 MECHATRONICS | Rental | 1.344
Raspberry Pi 4 4GB RAM | External | 1 | 0 | (blank) | 203 MECHATRONICS | Final Sale | 0
USB Micro-B power supply for RPI | External | 1 | 0 | (blank) | 205 MECHATRONICS | Final Sale | 0
Hex nut M3 pitch 0.5 | Nuts | 10 | 0.08 | (blank) | 23 HARDWARE |  | 0.8
M3 Locknut | Nuts | 75 | 0.09 | (blank) | 92 HARDWARE |  | 6.75
M3 pitch 0.50- 12mm | Machine screws | 15 | 0.07 | (blank) | 16 HARDWARE |  | 1.05
M3 pitch 0.50- 25mm | Machine screws | 25 | 0.12 | (blank) | 18 HARDWARE |  | 3
M3 pitch 0.50- 35mm | Machine screws | 15 | 0.14 | (blank) | 19 HARDWARE |  | 2.1
M3 pitch 0.50- 5mm | Machine screws | 40 | 0.09 | - | 12 HARDWARE |  | 3.6
M3 Washers | Washers | 10 | 0.02 | (blank) | 48 HARDWARE |  | 0.2
Notes:
Only modify the column Quantity
When done Print and submit the pdf
If met with error "The specified file is read only", close the purchase order that is open in the pdf viewer

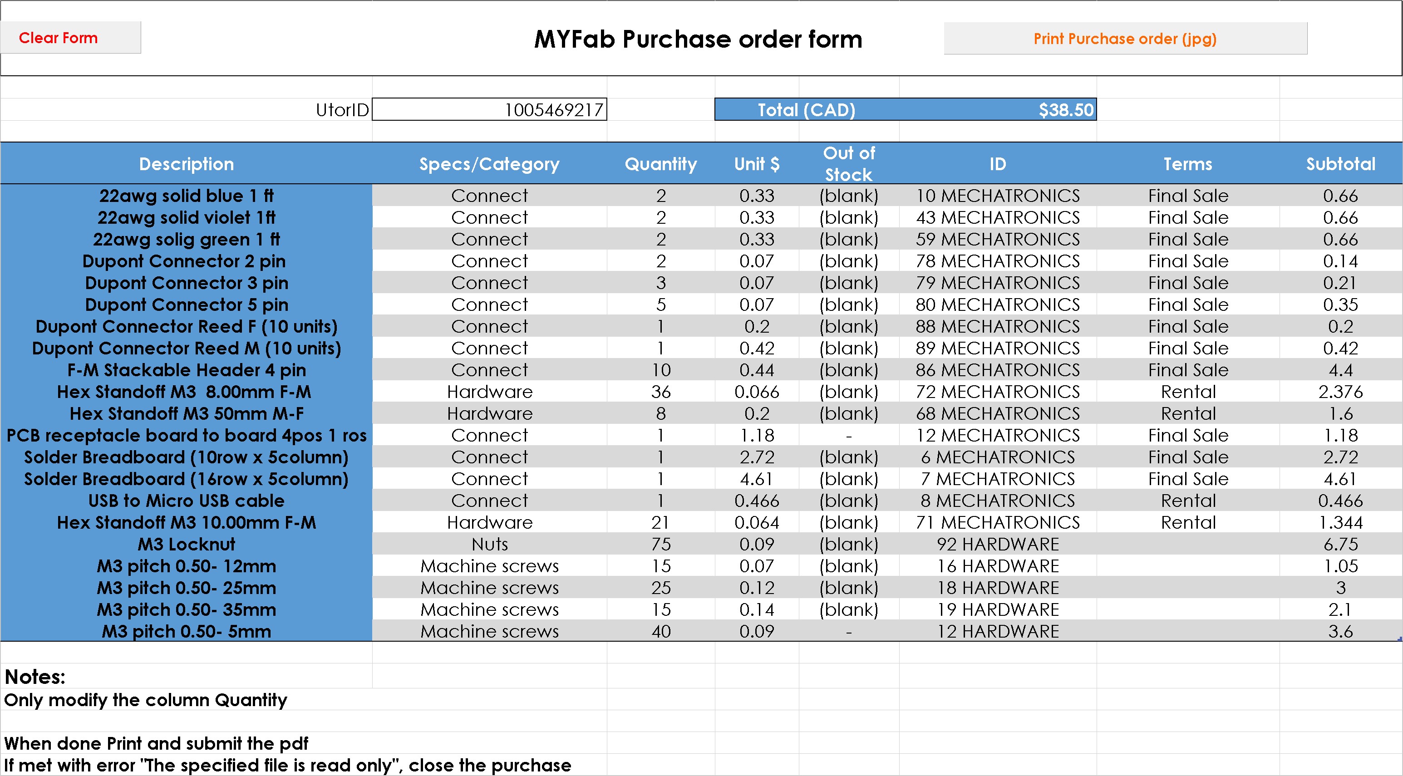
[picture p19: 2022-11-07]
Documents/MaterialOrders/MYFabOrder4-Team11.jpg

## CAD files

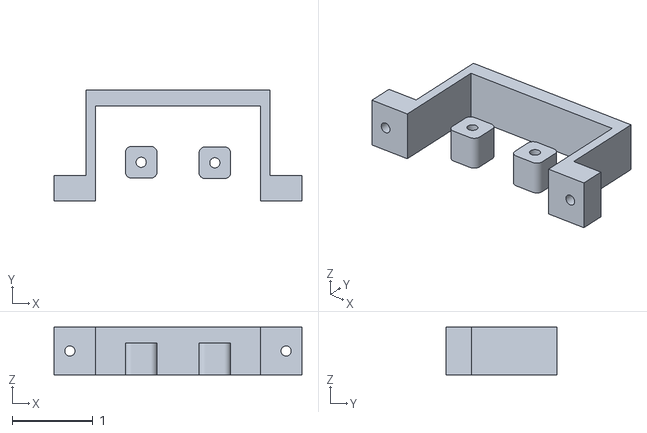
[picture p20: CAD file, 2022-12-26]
3DPrinting/Battery Mount V1 - 3D Print.stl
3.07 x 1.38 x 0.591

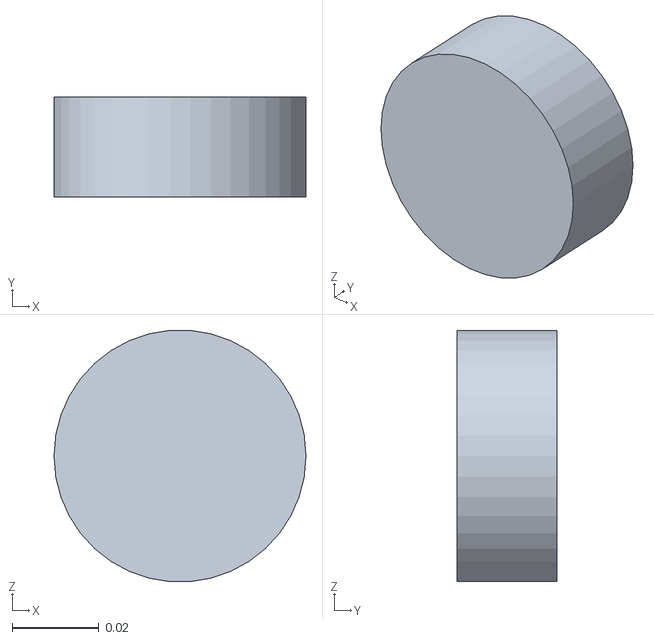
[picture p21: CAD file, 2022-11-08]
ROSMaster/worlds/models/robot/meshes/wheel1_link.STL
0.058 x 0.0231 x 0.0578

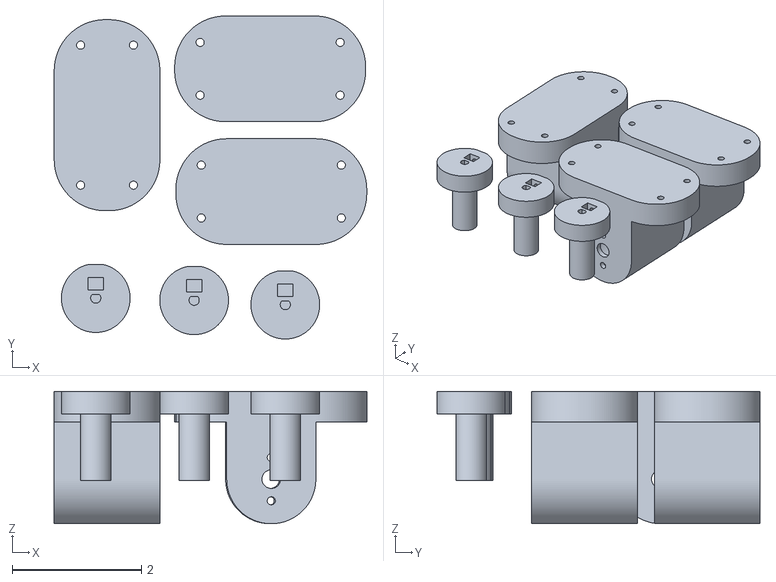
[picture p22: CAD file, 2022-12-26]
3DPrinting/Motor Mount V1 - 3D Print.stl
4.83 x 4.99 x 2.05

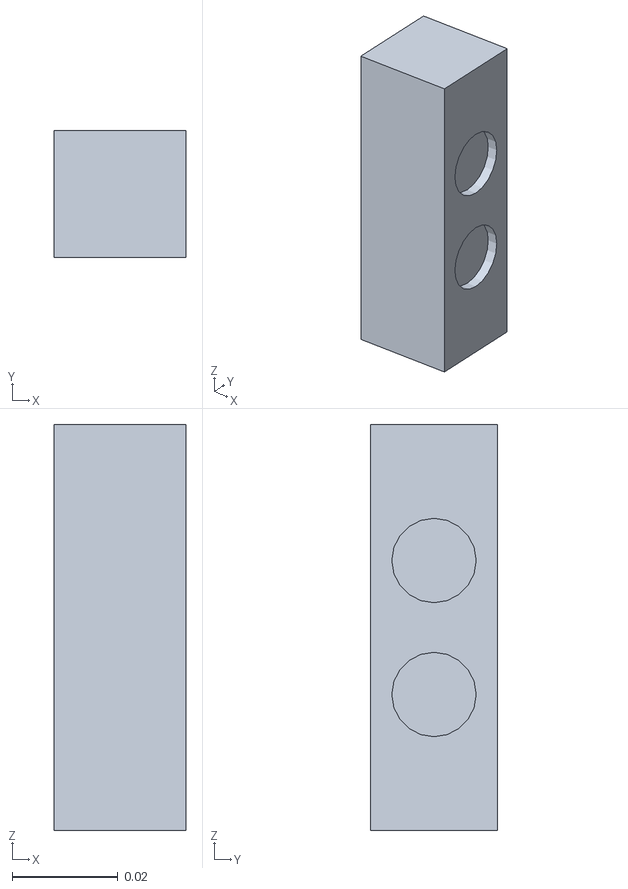
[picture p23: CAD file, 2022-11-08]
ROSMaster/worlds/models/robot/meshes/US3_link.STL
0.025 x 0.024 x 0.077

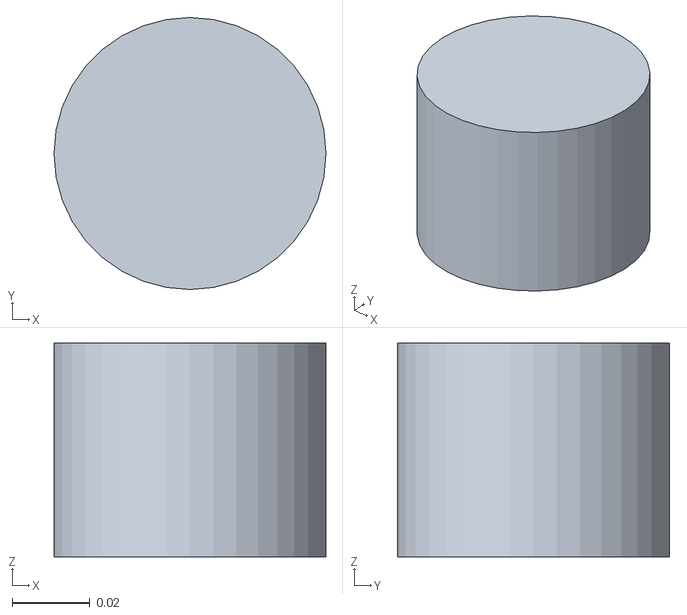
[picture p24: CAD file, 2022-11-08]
ROSMaster/worlds/models/robot/meshes/lidar_link.STL
0.07 x 0.07 x 0.055

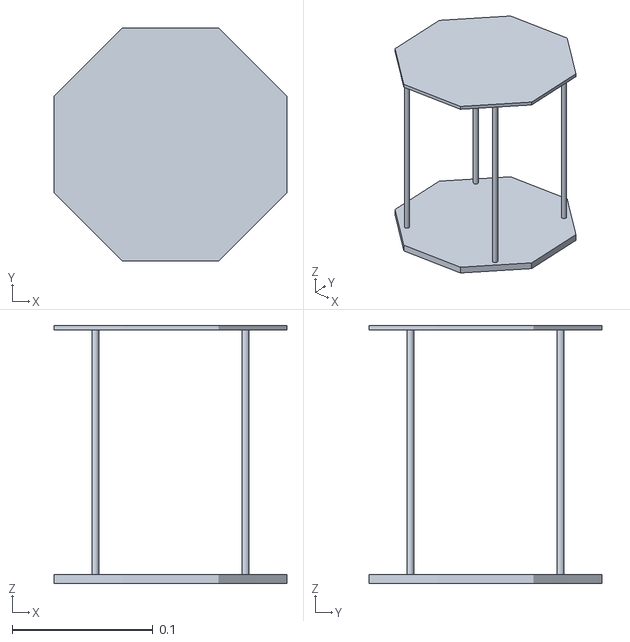
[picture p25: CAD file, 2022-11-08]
ROSMaster/worlds/models/robot/meshes/base_link.STL
0.165 x 0.165 x 0.183

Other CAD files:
ROSMaster/worlds/models/robot/meshes/wheel2_link.STL
ROSMaster/worlds/models/robot/meshes/US1_link.STL
ROSMaster/worlds/models/robot/meshes/wheel3_link.STL
ROSMaster/worlds/models/robot/meshes/US4_link.STL
ROSMaster/worlds/models/robot/meshes/US2_link.STL

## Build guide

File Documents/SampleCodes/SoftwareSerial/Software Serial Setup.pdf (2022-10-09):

# Software Serial Setup

# Arduino to Arduino Communication

## Interference on

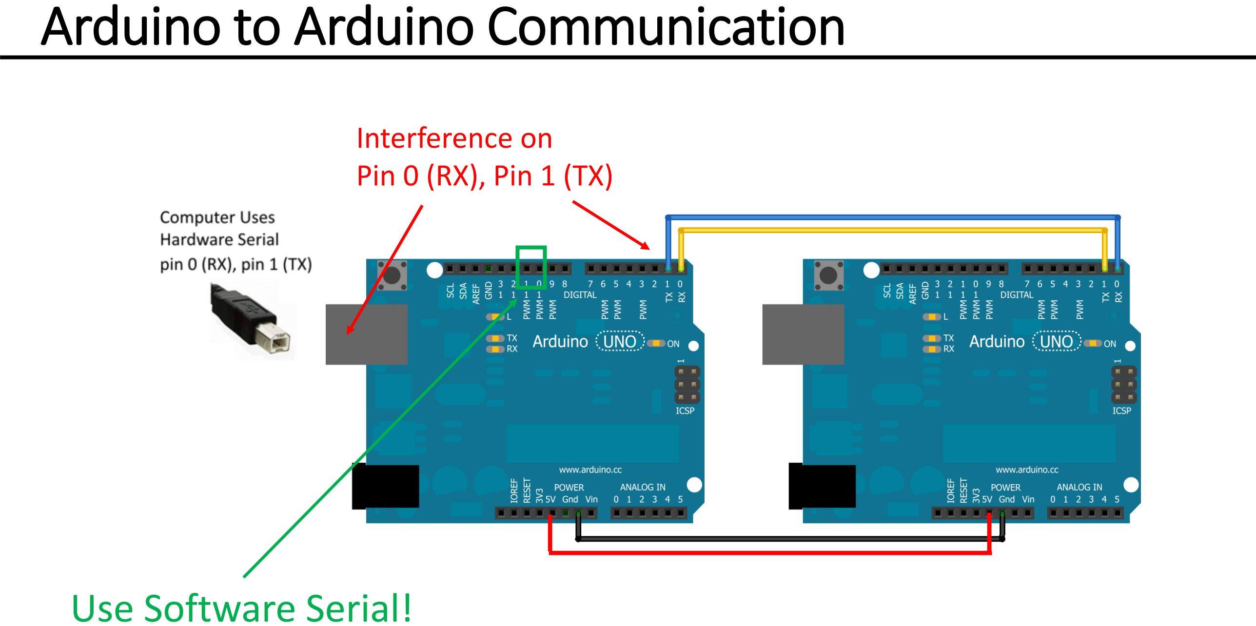
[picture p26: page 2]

## Pin 0 (RX), Pin 1 (TX)

# Use Software Serial!

# Arduino Sample Code

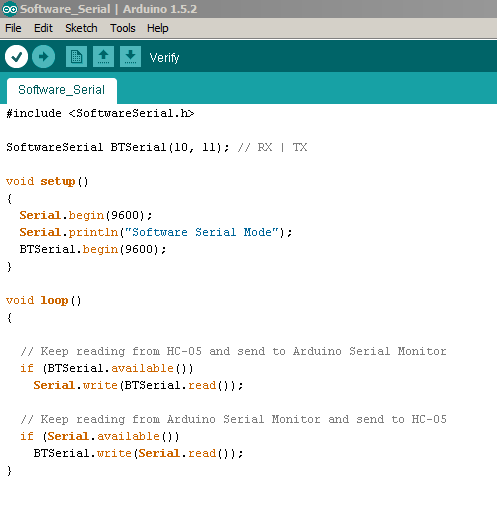
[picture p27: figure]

# Software Serial Wiring

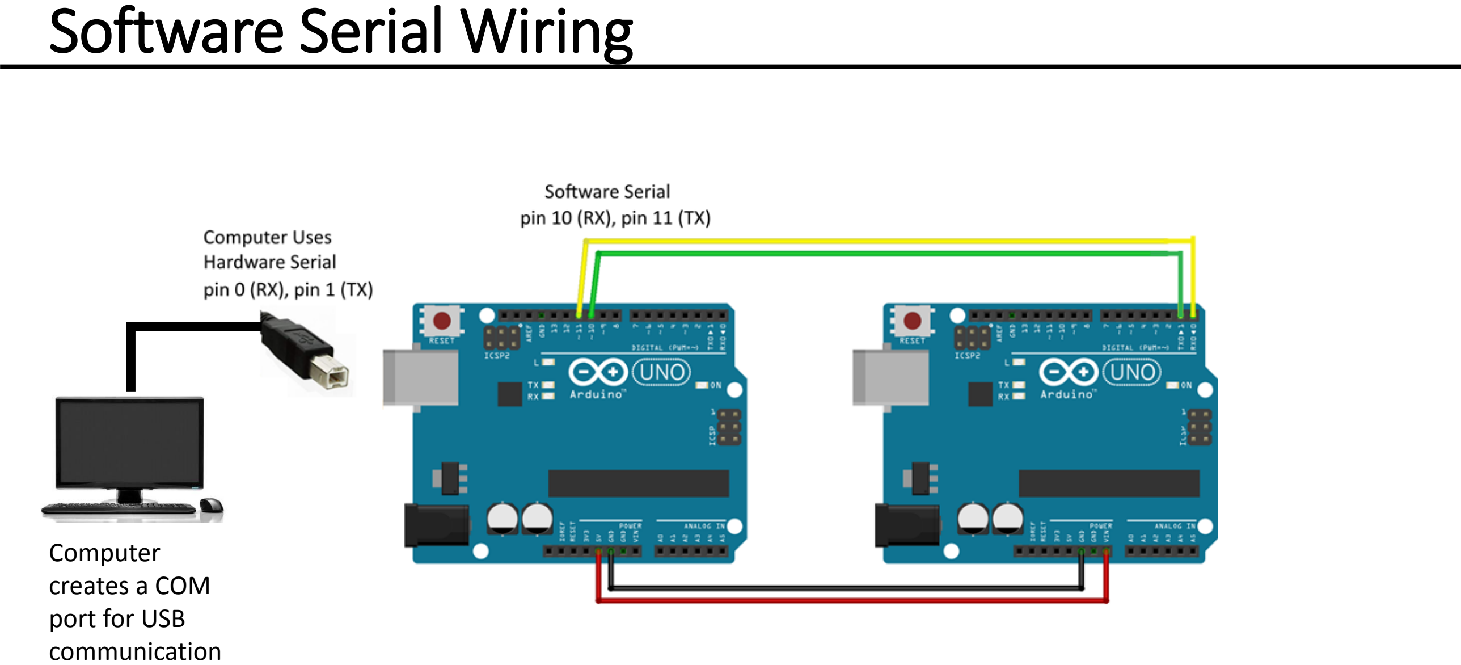
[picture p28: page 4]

Computer
creates a COM
port for USB
communication

# Replacing USB Cable with Bluetooth

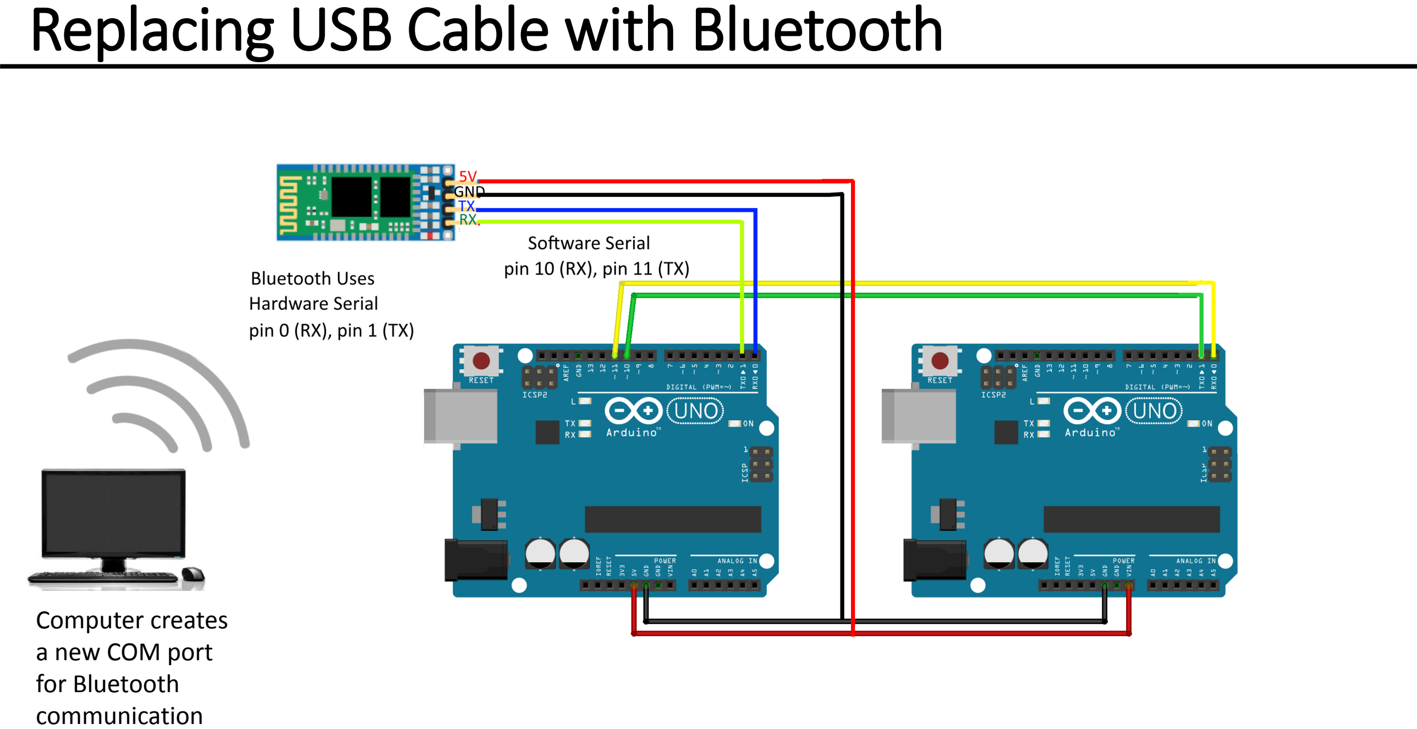
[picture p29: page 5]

Computer creates
a new COM port
for Bluetooth
communication

- Arduino code stays the same when changing from USB to Bluetooth.

## - How are the Arduino’s powered? If powering Arduino with a 12V battery, then connect to the Vin pin (or Plug), and the Arduino board’s

linear regulator will step down the voltage to 5V.

## - Ensure grounding pins are maintained across power supplies and

between the two Arduino’s.

## - If your robot is turned on and off frequently, the Bluetooth will need to reconnect each time. Consider powering Bluetooth with a separate

battery and 5V linear regulator to maintain the connection.

## - MATLAB communication is the same as for USB (see lab 4), just have

to find the COM port created for the Bluetooth.

# Additional Notes

# MATLAB Sample Code

serialInfo = instrhwinfo('serial');
comPorts = serialInfo.AvailableSerialPorts;

s = serial('COM4'); % creates serial object fopen(s); % connects to serial object pause(0.2);

fwrite(s,'r'); % writes letter to Arduino sample = fscanf(s); % reads from Arduino disp(sample);

fclose(s);

str = input('Input: ','s');
while str ~= 'q'

fwrite(s,str); % writes letter to Arduino
pause(0.5);
while s.bytesAvailable > 0 % recieve data from Arduino sample = fscanf(s); % reads from Arduino
end
disp(sample);

str = input('Input: ','s');
end

Alternatively, use a loop

MATLAB Communication over Serial (i.e. COM Port)

% if you don’t close COM
port after finishing you will need to restart MATLAB

repeat

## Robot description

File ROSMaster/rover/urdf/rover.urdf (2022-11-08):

<?xml version="1.0" encoding="utf-8"?>
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
<robot name="rover">
  <link name="base_link">
    <inertial>
      <origin xyz="9.58610261324536E-18 3.82610526269858E-18 0.064590953056216" rpy="0 0 0" />
      <mass value="0.229882969798051" />
      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
    </inertial>
    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
  </link>
  <link name="wheel1_link">
    <inertial>
      <origin xyz="3.9489E-17 -1.2917E-16 0.0057626" rpy="0 0 0" />
      <mass value="0.060901" />
      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
    </inertial>
    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
  </link>
  <joint name="wheel1_joint" type="continuous">
    <origin xyz="0.048665 0.08429 0" rpy="-1.5708 -0.38253 -0.5236" />
    <parent link="base_link" />
    <child link="wheel1_link" />
    <axis xyz="0 0 1" />
  </joint>
  <link name="wheel2_link">
    <inertial>
      <origin xyz="2.6725E-17 1.6435E-17 0.04488" rpy="0 0 0" />
      <mass value="0.060901" />
      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
    </inertial>
    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
  </link>
  <joint name="wheel2_joint" type="continuous">
    <origin xyz="0.029106 -0.050413 0" rpy="-1.5708 1.1361 -2.618" />
    <parent link="base_link" />
    <child link="wheel2_link" />
    <axis xyz="0 0 1" />
  </joint>
  <link name="wheel3_link">
    <inertial>
      <origin xyz="-2.1018E-17 -3.251E-17 0.011525" rpy="0 0 0" />
      <mass value="0.060901" />
      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
    </inertial>
    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
  </link>
  <joint name="wheel2_joint" type="continuous">
    <origin xyz="-0.091567 0 0" rpy="-1.5708 -0.39309 1.5708" />
    <parent link="base_link" />
    <child link="wheel3_link" />
    <axis xyz="0 0 1" />
  </joint>
  <link name="us1_link">
    <inertial>
      <origin xyz="0.012002 0.038481 0.012243" rpy="0 0 0" />
      <mass value="0.045149" />
      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
    </inertial>
    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
  </link>
  <joint name="us1_joint" type="fixed">
    <origin xyz="0.062644 -0.012065 0.10325" rpy="1.5708 0 1.5708" />
    <parent link="base_link" />
    <child link="us1_link" />
    <axis xyz="0 0 0" />
  </joint>
  <link name="us2_link">
    <inertial>
      <origin xyz="0.012002 0.038481 0.012243" rpy="0 0 0" />
      <mass value="0.045149" />
      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
    </inertial>
    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
  </link>
  <joint name="us2_joint" type="fixed">
    <origin xyz="-0.012002 -0.062644 0.10325" rpy="1.5708 0 0" />
    <parent link="base_link" />
    <child link="us2_link" />
    <axis xyz="0 0 0" />
  </joint>
  <link name="us3_link">
    <inertial>
      <origin xyz="0.012002 0.038481 0.012243" rpy="0 0 0" />
      <mass value="0.045149" />
      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
    </inertial>
    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
  </link>
  <joint name="us3_joint" type="fixed">
    <origin xyz="-0.062644 0.011938 0.10325" rpy="1.5708 0 -1.5708" />
    <parent link="base_link" />
    <child link="us3_link" />
    <axis xyz="0 0 0" />
  </joint>
  <link name="us4_link">
    <inertial>
      <origin xyz="0.012002 0.038481 0.012243" rpy="0 0 0" />
      <mass value="0.045149" />
      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
    </inertial>
    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
  </link>
  <joint name="us4_joint" type="fixed">
    <origin xyz="0.012002 0.062644 0.10325" rpy="1.5708 0 3.1416" />
    <parent link="base_link" />
    <child link="us4_link" />
    <axis xyz="0 0 0" />
  </joint>
  <link name="lidar_link">
    <inertial>
      <origin xyz="-6.9389E-18 0.0275 -8.6736E-19" rpy="0 0 0" />
      <mass value="0.21166" />
      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
    </inertial>
    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
  </link>
  <joint name="lidar_joint" type="continuous">
    <origin xyz="0.0067498 -0.036576 0.18339" rpy="1.5708 0 -1.1777" />
    <parent link="base_link" />
    <child link="lidar_link" />
    <axis xyz="0 1 0" />
  </joint>
</robot>

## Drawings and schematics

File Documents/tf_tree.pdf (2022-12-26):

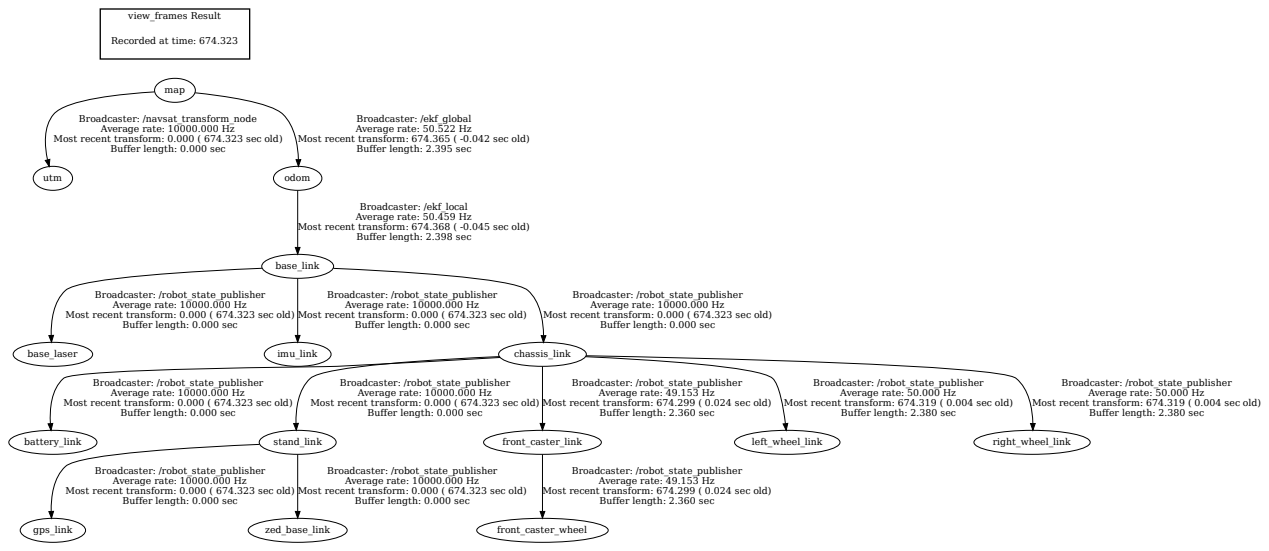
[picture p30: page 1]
view_frames Result; map; utm; odom; base_link; base_laser; imu_link; chassis_link; battery_link; stand_link; front_caster_link; left_wheel_link; right_wheel_link; gps_link; zed_base_link; front_caster_wheel

Recorded at time: 674.323

Broadcaster: /navsat_transform_node
Average rate: 10000.000 Hz
Buffer length: 0.000 sec

Broadcaster: /ekf_global
Average rate: 50.522 Hz
Buffer length: 2.395 sec

Most recent transform: 0.000 ( 674.323 sec old)

Most recent transform: 674.365 ( -0.042 sec old)

Broadcaster: /ekf_local
Average rate: 50.459 Hz
Buffer length: 2.398 sec

Most recent transform: 674.368 ( -0.045 sec old)

Broadcaster: /robot_state_publisher

Average rate: 49.153 Hz
Buffer length: 2.360 sec

Average rate: 50.000 Hz
Buffer length: 2.380 sec

Most recent transform: 674.299 ( 0.024 sec old)

Most recent transform: 674.319 ( 0.004 sec old)

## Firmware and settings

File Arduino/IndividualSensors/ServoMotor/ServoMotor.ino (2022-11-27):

#include <Servo.h>

Servo myservo;  // create servo object to control a servo
// twelve servo objects can be created on most boards

int pos = 0;    // variable to store the servo position

void setup() {
  myservo.attach(6);  // attaches the servo on pin 9 to the servo object
  myservo.write(180);
  delay(5000);
}

void loop() {
//  for (pos = 0; pos <= 180; pos += 1) { // goes from 0 degrees to 180 degrees
//    // in steps of 1 degree
//    myservo.write(pos);              // tell servo to go to position in variable 'pos'
//    delay(15);                       // waits 15ms for the servo to reach the position
//  }
//  for (pos = 180; pos >= 0; pos -= 1) { // goes from 180 degrees to 0 degrees
//    myservo.write(pos);              // tell servo to go to position in variable 'pos'
//    delay(15);                       // waits 15ms for the servo to reach the position
//  }
  myservo.write(0);
  delay(10000);
  myservo.write(180);
  while (1){
    int i = 1;
  }
}

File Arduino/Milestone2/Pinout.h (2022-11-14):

const uint8_t ENCODER1A = 2; //digital input
const uint8_t ENCODER1B = 5;
const uint8_t ENCODER2A = 3;
const uint8_t ENCODER2B = 6;
const uint8_t ENCODER3A = 4;
const uint8_t ENCODER3B = 7;

const uint8_t DIR1A = A0; //digital output
const uint8_t DIR1B = A1;
const uint8_t DIR2A = A2;
const uint8_t DIR2B = A3;
const uint8_t DIR3A = A4;
const uint8_t DIR3B = A5;

const uint8_t EN1 = 9; //analog output (PWM)
const uint8_t EN2 = 10;
const uint8_t EN3 = 11;

//TOF Sensor must be connected to SDA and SCL pins (address of 0x29)

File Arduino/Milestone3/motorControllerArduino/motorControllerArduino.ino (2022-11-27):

#include <ros.h>
#include "Pinout.h" // liam will modify pinout header to reflect electrnoics
#include <std_msgs/Int16MultiArray.h> // pwm data is sent as 16 bit array

ros::NodeHandle nh;


void messageCb(const std_msgs::Int16MultiArray& pwm_msg) {
//  mySerial.println("inside correct callback");
  digitalWrite(LED_BUILTIN, HIGH-digitalRead(LED_BUILTIN));
  digitalWrite(DIR1A, pwm_msg.data[0]);
  digitalWrite(DIR1B, !pwm_msg.data[0]);
  digitalWrite(DIR2A, pwm_msg.data[2]);
  digitalWrite(DIR2B, !pwm_msg.data[2]);
  digitalWrite(DIR3A, pwm_msg.data[4]);
  digitalWrite(DIR3B, !pwm_msg.data[4]);

  analogWrite(EN1, pwm_msg.data[1]);
  analogWrite(EN2, pwm_msg.data[3]+10);
  analogWrite(EN3, pwm_msg.data[5]);
}

ros::Subscriber<std_msgs::Int16MultiArray> sub("wheelsPWM", &messageCb );

void setup()
{
  nh.initNode();
  nh.subscribe(sub);
//  nh.subscribe(sub2);
  pinMode(LED_BUILTIN, OUTPUT);
  pinMode(EN1, OUTPUT);
  pinMode(EN2, OUTPUT);
  pinMode(EN3, OUTPUT);

  pinMode(DIR1A, OUTPUT);
  pinMode(DIR1B, OUTPUT);
  pinMode(DIR2A, OUTPUT);
  pinMode(DIR2B, OUTPUT);
  pinMode(DIR3A, OUTPUT);
  pinMode(DIR3B, OUTPUT);  
}

void loop()
{
  nh.spinOnce();
  delay(1);
}

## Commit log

2022-10-06 Add Simulation files
    [drive.csv, maze.csv, robot.csv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]
2022-10-06 Add Arduino blank files and header files
2022-10-07 Matlab file to determine motor speeds
    [drive.csv, maze.csv, robot.csv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]
2022-10-08 Begin architecture for Arduino as purely controller
2022-10-09 Completed skeleton of Arduino code and added classroom files
2022-11-01 New files for Blender URDF
    [Attempt1.blend, Lidar.SLDPRT, MaterialOrder_MyfabJPG_Team11.xlsm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]
2022-11-06 started world
    [model.sdf]
2022-11-06 Create Gazebo world launch file
    [model.sdf]
2022-11-07 first finish of world
    [Attempt1.blend, Attempt2.blend, MaterialOrder_MyfabJPG_Team11Mech.xlsm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]
2022-11-07 Working and sized world of maze
    [model.sdf]
2022-11-07 Finished wheelControl.cpp file for now
2022-11-08 first test urdf
    [base_link.STL, lidar_link.STL, rover.SLDASM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]
2022-11-08 failed import of urdf
    [base_link.STL, lidar_link.STL, rover.csv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]
2022-11-08 Finished URDF
    [Lidar.SLDPRT, US1_link.STL, US2_link.STL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]
2022-11-09 Created preliminary launch file for teleop
    [US1_link.STL, US2_link.STL, US3_link.STL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]
2022-11-09 Functional finished motor controller node
2022-11-09 Updated Matlab code and fixed motor controller logic
    [rover_urdf.SLDASM]
2022-11-09 motor node ouputs 6 elements with rpms
2022-11-10 Separated into 2 main files, prepared motor subscriber
2022-11-20 Chris update
    [lidar.xacro, robot.urdf.xacro, rover.urdf]
2022-11-20 Staging for Chris new branch
    [rover.urdf]
2022-11-20 Remvoed duplicate rover model
    [rover.urdf]
2022-11-20 for chris
    [rover.urdf]
2022-11-22 Functioning simulation Hector SLAM
    [rover.urdf]
2022-11-22 Working rviz visualization with config
    [rover.urdf]
2022-11-22 Fix Rviz configs
    [rover.urdf]
2022-11-27 Just got to MC on Sunday
    [rover.urdf]
2022-11-28 "fixed launch file, but mode1_nav still not working"
    [mode1_nav.py]
2022-12-26 Last save before computer dies
    [Attempt1.blend, Attempt2.blend, Lidar.SLDPRT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]
2022-12-26 Everything except Sweeper CAD files
    [Battery Mount V1 - 3D Print.stl, MaterialOrder_MyfabJPG_Team11.xlsm, MaterialOrder_MyfabJPG_Team11Mech.xlsm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]
